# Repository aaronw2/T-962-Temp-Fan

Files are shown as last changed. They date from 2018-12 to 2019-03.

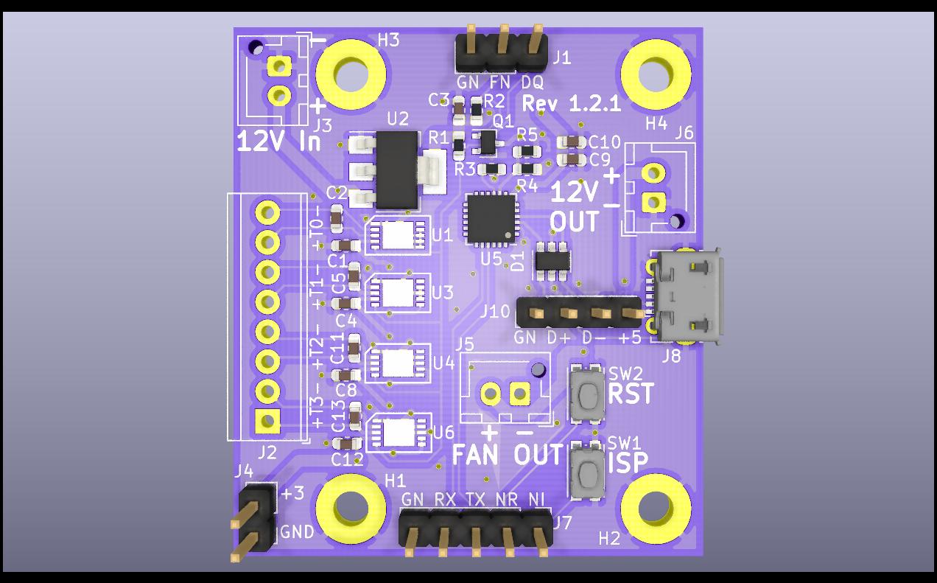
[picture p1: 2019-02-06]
Pictures/Front.jpg

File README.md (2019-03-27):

This board provides support for up to 4 K-type temperature probes as
well as fan PWM support and a USB to serial interface to enhance the
T-962 reflow oven.

Connectors:

J1: Connect to T962 controller board
1: DQ
2: FAN_PWM
3: GND

J2: Thermocouple connector
1: T3+
2: T3-
3: T2+
4: T2-
5: T1+
6: T1-
7: T0+
8: T0-

J3: 12V in
1: GND
2: +12V

J4: +3V out
1: GND
2: +3V

J5: Fan out
1: PWM (GND)
2: +12V

J6: +12V out
1: GND
2: +12V

J7: Programming Header, connect to T962 controller board header
1: N_ISP
2: N_RST
3: TX
4: RX
5: GND

Hook up either J8 or J10, not both

J8: Micro USB

J9: N_ISP and N_RST for external buttons
1: N_RST
2: GND
3: N_ISP

J10: USB
1: GND
2: D+
3: D-
4: +5V

BOM:
QTY Ref
5   C1,C4,C8,C10,C12: 0.1uf X7R 0603
4   C2,C5,C11,C13 0.01uF X7R 0603
1   C3 1uF X7R 0603
1   C9 4.7uF X7R 0603
1   D1: ST Microelectronics USBLC6-2SC6
1   J2: TE 282834-8
1   J3, J5, J6: JST XH-B02B-XH-AM
1   J8: Molex 105017-0001
1   Q1: Infineon BSS214NWH6327XTSA1
1   R1: 4.7K 0603
1   R2: 100K 0603
1   R3: 1K 0603
1   R4: 22.1K 0603
1   R5: 47.5K 0603
2   S1, S2: C&K KMR231NG LFS
4   U1, U3, U4, U6: Maxim MAX31850KATB+
1   U2: ST Microelectronics LD1117S33CTR
1   U5: Silicon Labs CP2102N-A01-QFN24

All parts can be found at Digikey, however the MAX31850KATB+ is considerably
less expensive at Mouser.

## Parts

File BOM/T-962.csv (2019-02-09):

Refs | Value | Footprint | Quantity | MFR | MPN | SPR | SPN
U5 | CP2102N-A01-QFN24 | Aaron:QFN-24-1EP_4x4mm_Pitch0.5mm_rounded_corners | 1 | Silicon Labs | CP2102N-A01-GQFN24R | Digikey | 336-4737-1-ND
SW1;SW2 | SW_SPST_KMR2 | Aaron:SW_SPST_KMR2 | 2 | C&K | KMR231NG LFS | Digikey | CKN10246CT-ND
U1;U3;U4;U6 | MAX31850KATB+ | Aaron:TDFN-10_3x4mm_P0.5mm | 4 | Maxim | MAX31850KATB+ | Digikey | MAX31850KATB+-ND
J8 | USB_B_Micro | Aaron:USB_Micro-B_Molex-105017-0001 | 1 | Molex | 1050170001 | Digikey | WM1399CT-ND
C2;C5;C11;C13 | 0.01uF | Capacitor_SMD:C_0603_1608Metric | 4 | - | - | - | -
C1;C4;C8;C12;C10 | 0.1uF | Capacitor_SMD:C_0603_1608Metric | 5 | - | - | - | -
C3 | 1uF | Capacitor_SMD:C_0603_1608Metric | 1 | - | - | - | -
C9 | 4.7uF | Capacitor_SMD:C_0603_1608Metric | 1 | - | - | - | -
J3;J5;J6 | JST XH-B02B-XH-AM | Connector_JST:JST_XH_B02B-XH-AM_1x02_P2.50mm_Vertical | 3 | JST | B2B-XH-A(LF)(SN) | Digikey | 455-2247-ND
J4 | Conn_01x02_Male | Connector_PinHeader_2.54mm:PinHeader_1x02_P2.54mm_Vertical | 1 | - | - | - | -
J1 | Conn_01x03 | Connector_PinHeader_2.54mm:PinHeader_1x03_P2.54mm_Vertical | 1 | - | - | - | -
J10 | Conn_01x04 | Connector_PinHeader_2.54mm:PinHeader_1x04_P2.54mm_Vertical | 1 | - | - | - | -
J7 | 2.54mm pin header | Connector_PinHeader_2.54mm:PinHeader_1x05_P2.54mm_Vertical | 1 | - | - | - | -
H1;H2;H3;H4 | MountingHole_Pad | MountingHole:MountingHole_3mm_Pad | 4 | - | - | - | -
U2 | LD1117S33CTR | Package_TO_SOT_SMD:SOT-223 | 1 | STMicroelectronics | LD1117S33CTR | Digikey | 497-1241-1-ND
D1 | USBLC6-2SC6 | Package_TO_SOT_SMD:SOT-23-6 | 1 | STMicroelectronics | USBLC6-2SC6 | Digikey | 497-5235-1-ND
Q1 | BSS214NW | Package_TO_SOT_SMD:SOT-323_SC-70 | 1 | Infineon | BSS214NWH6327XTSA1 | Digikey | BSS214NWH6327XTSA1CT-ND
R2 | 100K | Resistor_SMD:R_0603_1608Metric | 1 | Yageo | AC0603FR-07100KL | Digikey | 311-100KLDCT-ND
R3 | 1K | Resistor_SMD:R_0603_1608Metric | 1 | Yageo | RC0603FR-071KL | Digikey | 311-1.00KHRCT-ND
R4 | 22.1K | Resistor_SMD:R_0603_1608Metric | 1 | Panasonic | ERJ-3EKF2212V | Digikey | P22.1KHCT-ND
R1 | 4.7K | Resistor_SMD:R_0603_1608Metric | 1 | Yageo | RC0603FR-074K7L | Digikey | 311-4.70KHRCT-ND
R5 | 47.5K | Resistor_SMD:R_0603_1608Metric | 1 | Yageo | RC0603FR-0747K5L | Digikey | 311-47.5KHRCT-ND
J2 | TE 282834-8 | TerminalBlock_TE-Connectivity:TerminalBlock_TE_282834-8_1x08_P2.54mm_Horizontal | 1 | TE | 282834-8 | Digikey | A98338-ND

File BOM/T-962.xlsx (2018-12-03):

Refs | Value | Footprint | Quantity | MFR | MPN | SPR | SPN
U5 | CP2102N-A01-QFN24 | Aaron:QFN-24-1EP_4x4mm_Pitch0.5mm_rounded_corners | 1 | Silicon Labs | CP2102N-A01-GQFN24R | Digikey | 336-4737-1-ND
SW1;SW2 | SW_SPST_KMR2 | Aaron:SW_SPST_KMR2 | 2 | C&K | KMR231NG LFS | Digikey | CKN10246CT-ND
U1;U3;U4;U6 | MAX31850KATB+ | Aaron:TDFN-10_3x4mm_P0.5mm | 4 | Maxim | MAX31850KATB+ | Digikey | MAX31850KATB+-ND
J8 | USB_B_Micro | Aaron:USB_Micro-B_Molex-105017-0001 | 1 | Molex | 1050170001 | Digikey | WM1399CT-ND
C2;C5;C11;C13 | 0.01uF | Capacitor_SMD:C_0603_1608Metric | 4 | Samsung | CL10B103KB8NCNC | Digikey | 1276-1921-1-ND
C1;C4;C8;C12;C7;C10 | 0.1uF | Capacitor_SMD:C_0603_1608Metric | 6 | Samsung | CL10B104KO8WPNC | Digikey | 1276-6582-1-ND
C3 | 1uF | Capacitor_SMD:C_0603_1608Metric | 1 | Samsung | CL10B105MO8NNWC | Digikey | 1276-6524-1-ND
C6;C9 | 4.7uF | Capacitor_SMD:C_0603_1608Metric | 2 | Samsung | CL10B475KQ8NQNC | Digikey | 1276-2087-1-ND
J3;J5 | B2B-XH-A(LF)(SN) | Connector_JST:JST_XH_B02B-XH-AM_1x02_P2.50mm_Vertical | 2 | JST | B2B-XH-A(LF)(SN) | Digikey | 455-2247-ND
J1 | 2.54mm pin header | Connector_PinHeader_2.54mm:PinHeader_1x03_P2.54mm_Vertical | 1 | - | - | - | -
J10 | Conn_01x04 | Connector_PinHeader_2.54mm:PinHeader_1x04_P2.54mm_Vertical | 1 | - | - | - | -
J7 | 2.54mm pin header | Connector_PinHeader_2.54mm:PinHeader_1x05_P2.54mm_Vertical | 1 | - | - | - | -
H1;H2;H3;H4 | MountingHole_Pad | MountingHole:MountingHole_3mm_Pad | 4 | - | - | - | -
U2 | LD1117S33CTR | Package_TO_SOT_SMD:SOT-223 | 1 | ST Microelectronics | LD1117S33CTR | Digikey | 497-1241-1-ND
Q1 | BSS214NW | Package_TO_SOT_SMD:SOT-323_SC-70 | 1 | Infineon | BSS214NWH6327XTSA1 | Digikey | BSS214NWH6327XTSA1CT-ND
D1 | USBLC6-2SC6 | Package_TO_SOT_SMD:SOT-666 | 1 | STMicroelectronics | USBLC6-2SC6 | Digikey | 497-5235-1-ND
R2 | 100K | Resistor_SMD:R_0603_1608Metric | 1 | Yageo | AC0603FR-07100KL | Digikey | 311-100KLDCT-ND
R3 | 1K | Resistor_SMD:R_0603_1608Metric | 1 | Yageo | RC0603FR-071KL | Digikey | 311-1.00KHRCT-ND
R4 | 22.1K | Resistor_SMD:R_0603_1608Metric | 1 | Panasonic | ERJ-3EKF2212V | Digikey | P22.1KHCT-ND
R1 | 4.7K | Resistor_SMD:R_0603_1608Metric | 1 | Yageo | RC0603FR-074K7L | Digikey | 311-4.70KHRCT-ND
R5 | 47.5K | Resistor_SMD:R_0603_1608Metric | 1 | Yageo | RC0603FR-0747K5L | Digikey | 311-47.5KHRCT-ND
J2 | TE 282834-8 | TerminalBlock_TE-Connectivity:TerminalBlock_TE_282834-8_1x08_P2.54mm_Horizontal | 1 | TE | 282834-8 | Digikey | A98338-ND

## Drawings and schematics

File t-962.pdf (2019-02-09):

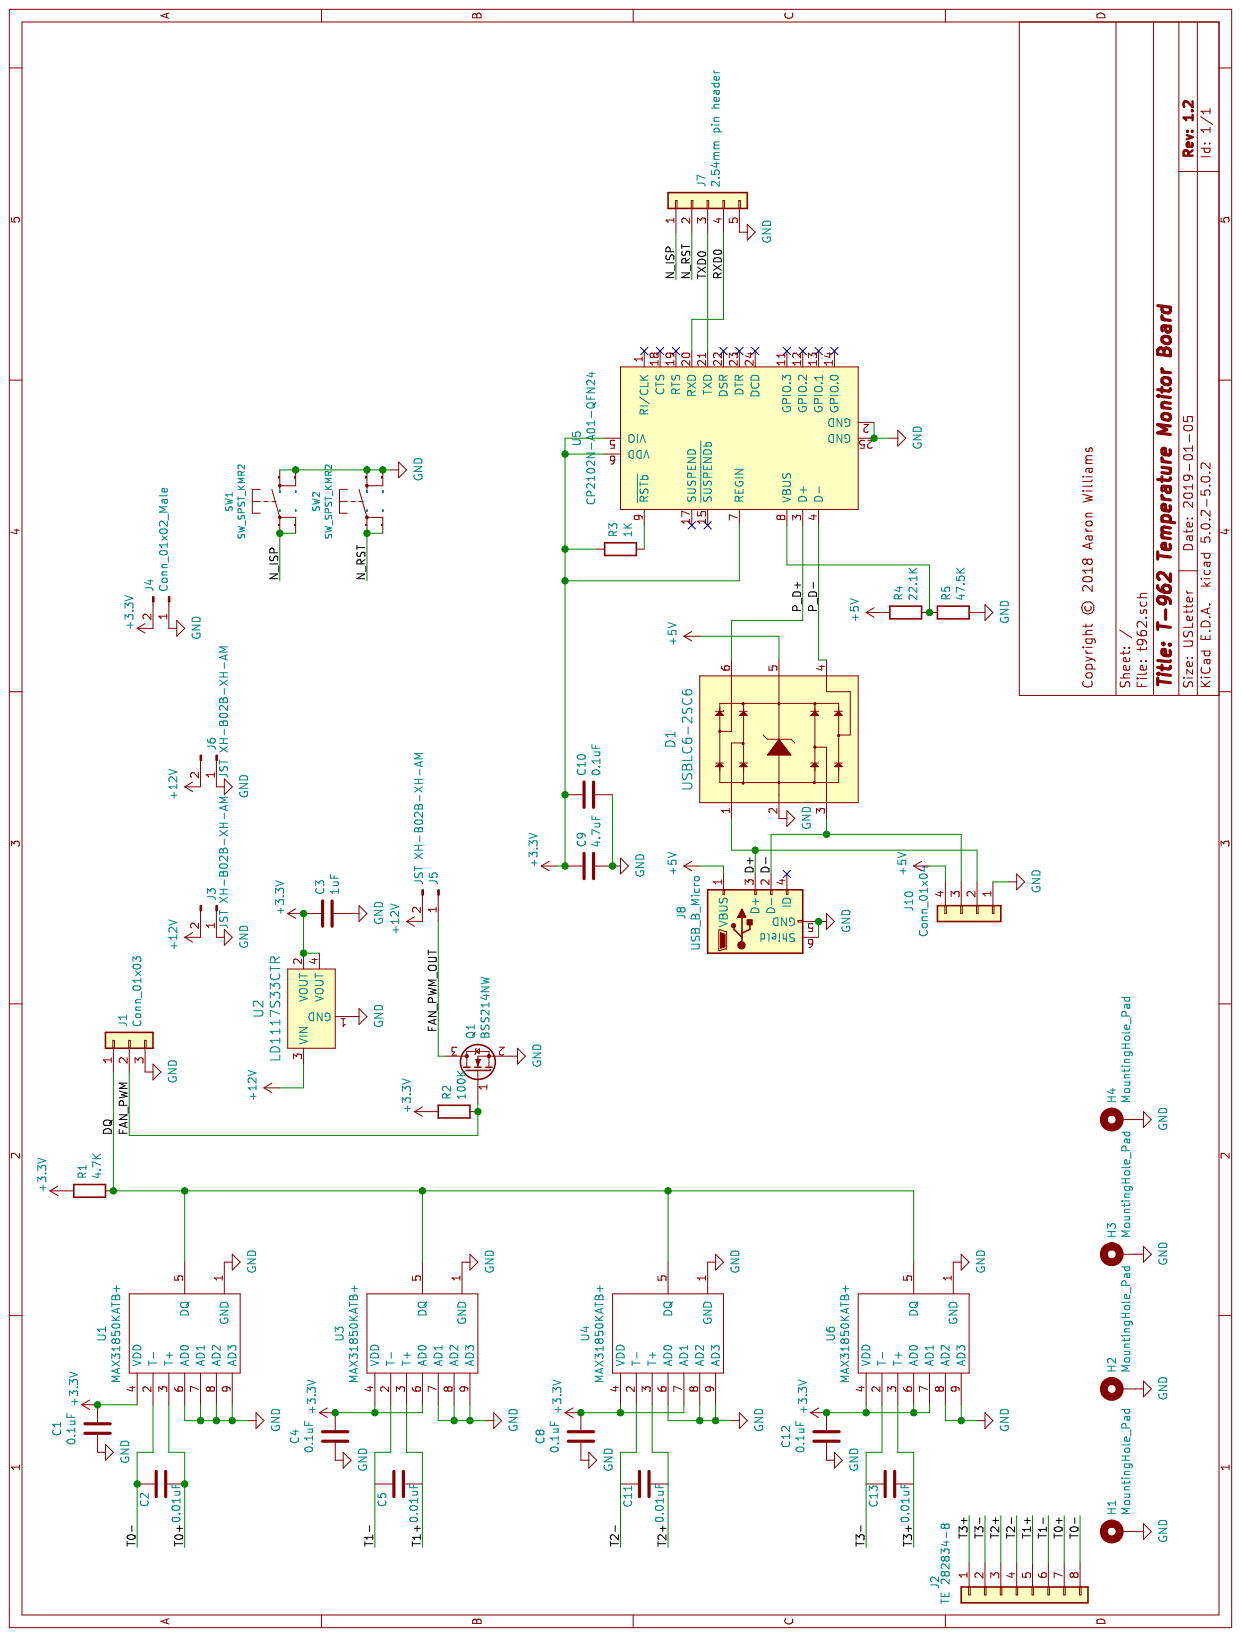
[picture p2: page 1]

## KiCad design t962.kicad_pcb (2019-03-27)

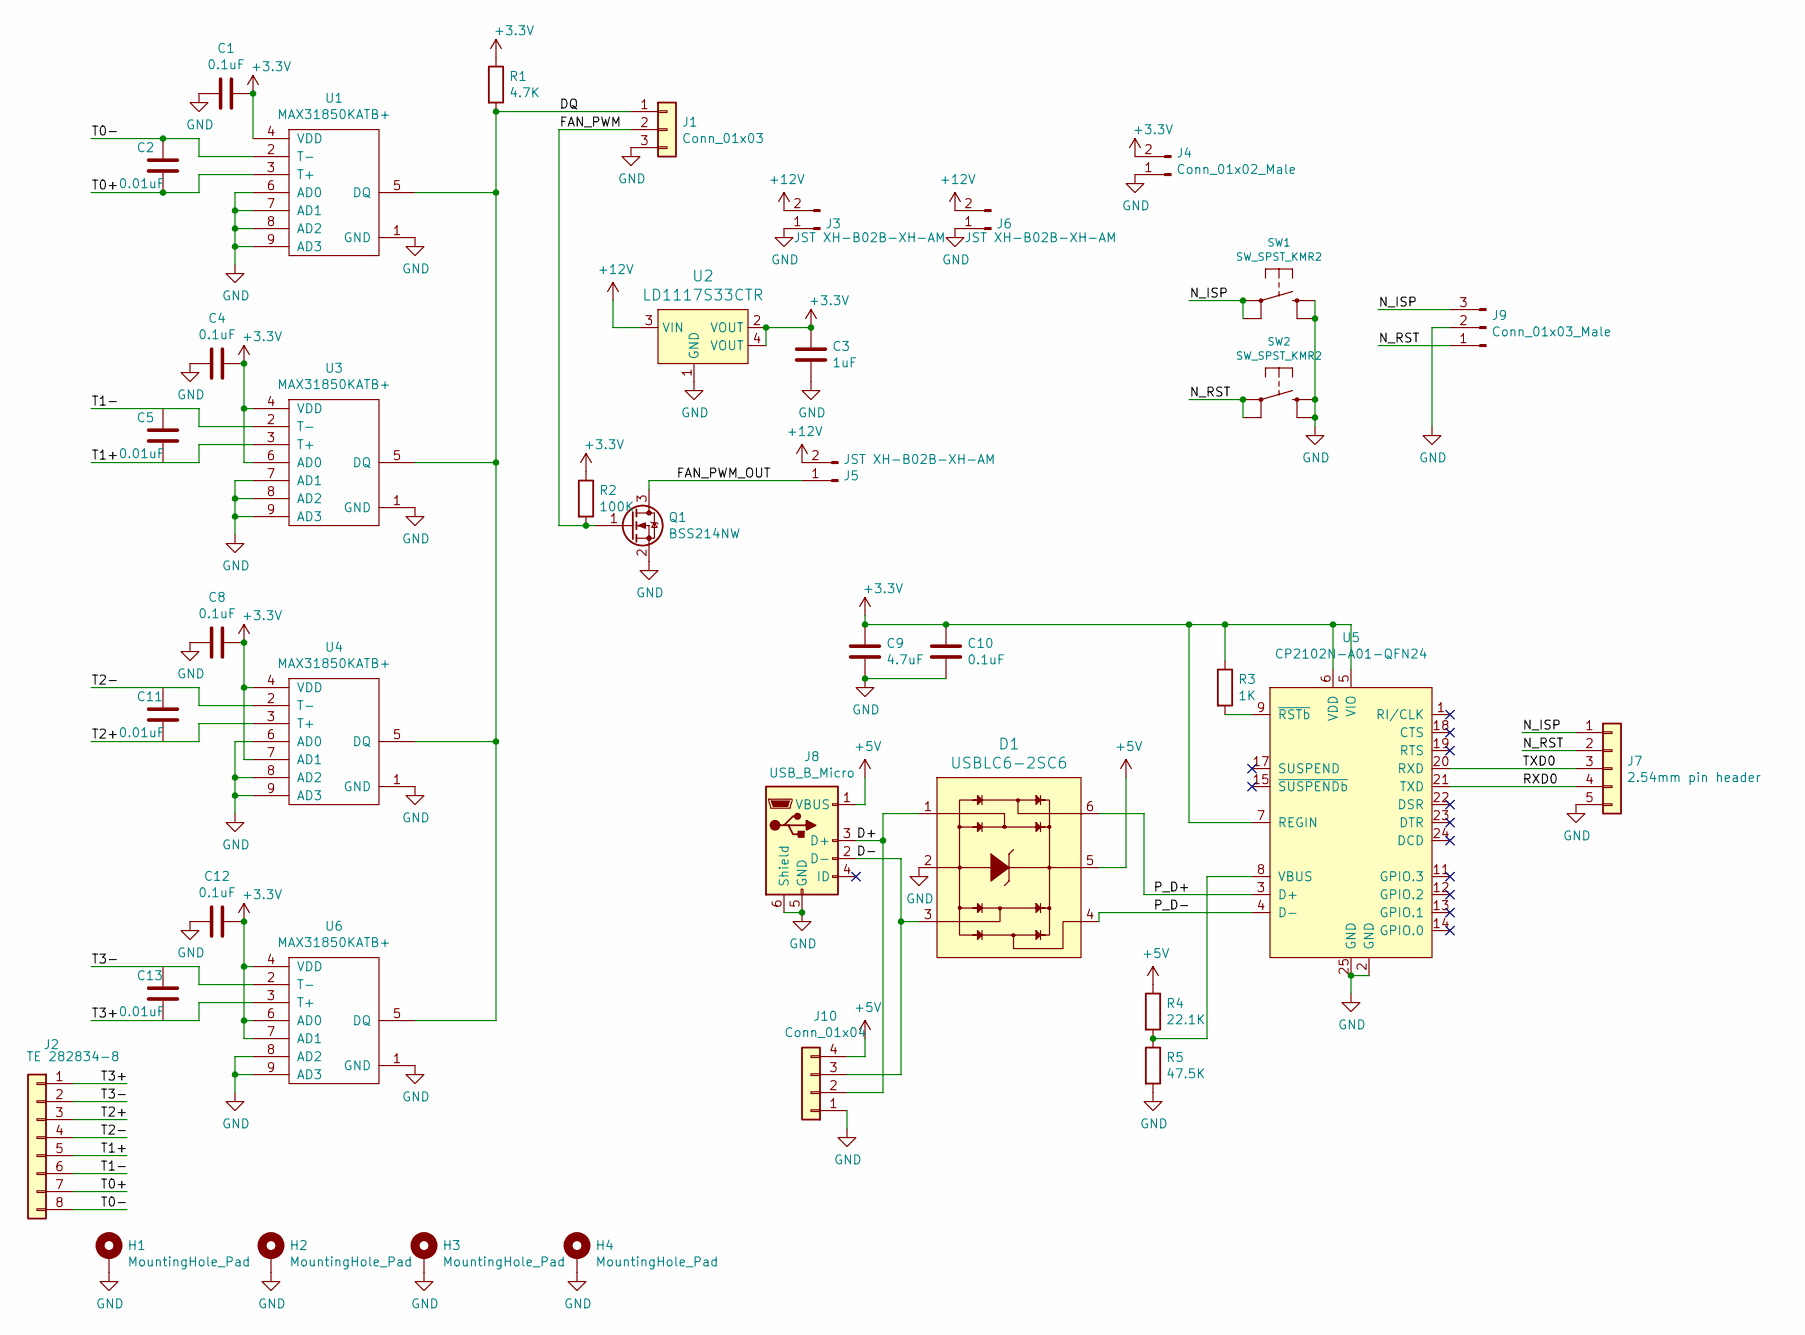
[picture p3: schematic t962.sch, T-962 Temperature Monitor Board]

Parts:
C1, C4, C8, C10, C12: 0.1uF; C_0603_1608Metric
C2, C5, C11, C13: 0.01uF; C_0603_1608Metric
C3: 1uF; C_0603_1608Metric
C9: 4.7uF; C_0603_1608Metric
D1: USBLC6-2SC6; SOT-23-6; MPN USBLC6-2SC6; Digi-Key_PN 497-5235-1-ND
H1, H2, H3, H4: MountingHole_Pad; MountingHole_3mm_Pad
J1: Conn_01x03; PinHeader_1x03_P2.54mm_Vertical
J2: TE 282834-8; TerminalBlock_TE_282834-8_1x08_P2.54mm_Horizontal; MPN 282834-8
J3, J5, J6: JST XH-B02B-XH-AM; JST_XH_B02B-XH-AM_1x02_P2.50mm_Vertical; MPN B2B-XH-A(LF)(SN)
J4: Conn_01x02_Male; PinHeader_1x02_P2.54mm_Vertical
J7: 2.54mm pin header; PinHeader_1x05_P2.54mm_Vertical
J8: USB_B_Micro; USB_Micro-B_Molex-105017-0001; MPN 1050170001
J9: Conn_01x03_Male; PinHeader_1x03_P2.54mm_Vertical
J10: Conn_01x04; PinHeader_1x04_P2.54mm_Vertical
Q1: BSS214NW; SOT-323_SC-70; MPN BSS214NWH6327XTSA1
R1: 4.7K; R_0603_1608Metric; MPN RC0603FR-074K7L
R2: 100K; R_0603_1608Metric; MPN AC0603FR-07100KL
R3: 1K; R_0603_1608Metric; MPN RC0603FR-071KL
R4: 22.1K; R_0603_1608Metric; MPN ERJ-3EKF2212V
R5: 47.5K; R_0603_1608Metric; MPN RC0603FR-0747K5L
SW1, SW2: SW_SPST_KMR2; MPN KMR231NG LFS
U1, U3, U4, U6: MAX31850KATB+; TDFN-10_3x4mm_P0.5mm; MPN MAX31850KATB+
U2: LD1117S33CTR; SOT-223; MPN LD1117S33CTR; Digi-Key_PN 497-1241-1-ND
U5: CP2102N-A01-QFN24; QFN-24-1EP_4x4mm_Pitch0.5mm_rounded_corners; MPN CP2102N-A01-GQFN24R

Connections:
+3V3: C1.2, C3.1, C4.2, C8.2, C9.1, C10.1, C12.2, J4.2, R1.1, R2.1, R3.1, U1.4 (VDD), U2.2 (VOUT), U2.4 (VOUT), U3.4 (VDD), U3.6 (AD0), U4.4 (VDD), U4.7 (AD1), U5.5 (VIO), U5.6 (VDD), U5.7 (REGIN), U6.4 (VDD), U6.6 (AD0), U6.7 (AD1)
+5V: D1.5, J8.1 (VBUS), J10.4, R4.1
+12V: J3.2, J5.2, J6.2, U2.3 (VIN)
/D+: D1.1, J8.3 (D+), J10.2
/D-: D1.3, J8.2 (D-), J10.3
/DQ: J1.1, R1.2, U1.5 (DQ), U3.5 (DQ), U4.5 (DQ), U6.5 (DQ)
/FAN_PWM: J1.2, Q1.1 (G), R2.2
/FAN_PWM_OUT: J5.1, Q1.3 (D)
/N_ISP: J7.1, J9.3, SW1.1
/N_RST: J7.2, J9.1, SW2.1
/P_D+: D1.6, U5.3 (D+)
/P_D-: D1.4, U5.4 (D-)
/RXD0: J7.4, U5.21 (TXD)
/T0+: C2.1, J2.7, U1.3 (T+)
/T0-: C2.2, J2.8, U1.2 (T-)
/T1+: C5.1, J2.5, U3.3 (T+)
/T1-: C5.2, J2.6, U3.2 (T-)
/T2+: C11.1, J2.3, U4.3 (T+)
/T2-: C11.2, J2.4, U4.2 (T-)
/T3+: C13.1, J2.1, U6.3 (T+)
/T3-: C13.2, J2.2, U6.2 (T-)
/TXD0: J7.3, U5.20 (RXD)
GND: C1.1, C3.2, C4.1, C8.1, C9.2, C10.2, C12.1, D1.2, H1.1, H2.1, H3.1, H4.1, J1.3, J3.1, J4.1, J6.1, J7.5, J8.5 (GND), J8.6 (Shield), J9.2, J10.1, Q1.2 (S), R5.2, SW1.2 (S), SW2.2 (S), U1.1 (GND), U1.6 (AD0), U1.7 (AD1), U1.8 (AD2), U1.9 (AD3), U1.11 (GND), U2.1 (GND), U3.1 (GND), U3.7 (AD1), U3.8 (AD2), U3.9 (AD3), U3.11 (GND), U4.1 (GND), U4.6 (AD0), U4.8 (AD2), U4.9 (AD3), U4.11 (GND), U5.2 (GND), U5.25 (GND), U6.1 (GND), U6.8 (AD2), U6.9 (AD3), U6.11 (GND)
unnamed: R3.2, U5.9 (~RSTb)
unnamed: R4.2, R5.1, U5.8 (VBUS)

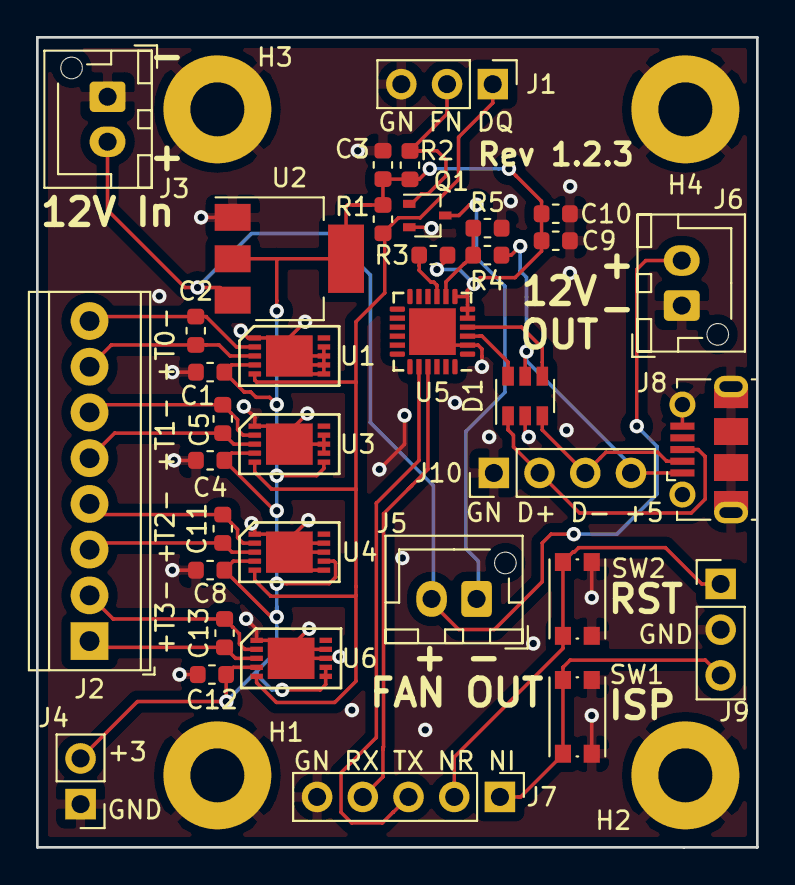
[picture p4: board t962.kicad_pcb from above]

Board: 2 copper layers, 40.0 x 45.0 mm, 40 parts (0 on the bottom side), 25 nets.

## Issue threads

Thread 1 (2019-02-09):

Can you provide a PDF of the schematic please

rolandking, 2019-02-09:
Looks like a nice project - thanks very much for sharing it.

Attempting to load up in kicad I have version mismatches and library issues which I suspect might not be that uncommon (I'm still on kicad 4.x). You provide the gerbers which is great, can you PDF up the schematic and upload that too please so people without kicad, or without a compatible version of kicad, can read, understand and build the project.

Thanks very much.

aaronw2, 2019-02-09:
Done. Note that my gerbers may have been out of date and I may have screwed up on the minimum solder mask width. Anyway, all should be good now and I also included a PDF of the schematic. This was done using KiCad 5.0.2 and I have my own libraries for some of these parts.

All parts can be found on Digikey, though the MAX31850s are a lot cheaper from Mouser.

Closed 2019-02-09.

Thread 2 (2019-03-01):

RXD/TXD maybe flipped?

metaneutrons, 2019-03-01:
Hi there, thanks for sharing your board. I already forked it and wonder if you maybe have flipped RXD/TXD connected to CP2102N? All other schematics have TX/RX crossed...

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

aaronw2, 2019-03-01:
Hi,

It's possible. I haven't had time to try and test that part out. It's easy to fix that in post fortunately, but I'll make the change.

-Aaron

aaronw2, 2019-03-27:
I have swapped TX and RX in rev 1.2.3 in addition to bringing out N_ISP and N_RST to another connector. No changes are required for the template.

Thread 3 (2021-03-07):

What happend on F3 page with 4 TC connected ?

zian31, 2021-03-07:
Hi,
If possible, have you a photo of the T-962 LCD (UnifiedEngineering) F3 page (Manual Mode) with 4 TC connected (and no DS18B20 connected for cold junction) ?
The AIR LEFT and RIGHT temperatures should be presents, but can we also see TRAY LEFT and RIGHT temp ?
An average of AIR LEFT & RIGHT is also shown ? Or an average of the 4 TC ?
Or maybe an average of the TRAY LEFT & RIGHT, which should be logical (moreover if this average is taken as the Temperature for the PID).
Thanks a lot for your answer, I'm asking it before making this modification.

zian31, 2021-03-10:
Answered here : https://github.com/UnifiedEngineering/T-962-improvements/issues/157

Closed 2021-03-10.

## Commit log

2018-11-17 Initial commit.
    [T-962.csv, T-962.xlsx, t962.kicad_pcb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]
2018-11-18 Added more part number information.
    [t962.sch]
2018-12-03 Fixed 12V connectors and USB to serial
    This swaps +12 and GND on the 12V and fan connectors and adds a second
    12v connector for bypassing the fan control if desired. Additionally,
    the SI2102N is now powered from the 3.3V supply instead of the USB bus.
    Updated to revision 1.1.
    [t962.kicad_pcb, t962.sch]
2018-12-03 Updated BOM
    [T-962.xlsx, t962.kicad_pcb, t962.sch]
2018-12-03 Added gerber files.
    [t962-B.Cu.gbr, t962-B.Mask.gbr, t962-B.SilkS.gbr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]
2019-01-05 This fixes the VIO input so it is properly powered. Additionally, the footprint for the USBLC6-2SC6 has been fixed to a SOT23-6 which is a bigger footprint than the SOT666 that was there.
    [t962-B.Cu.gbr, t962-B.Mask.gbr, t962-B.SilkS.gbr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]
2019-01-26 Fixed solder mask clearance.
    [t962.kicad_pcb]
2019-02-06 Fixed solder mask again and included pictures.
    [t962.kicad_pcb]
2019-02-09 Fixed pad mask clearance.
    [t962.kicad_pcb]
2019-02-09 Added PDF of schematic.
2019-02-09 Fixed solder mask min width again.
    [t962.kicad_pcb]
2019-02-09 Updated gerbers to match.
    [t962-B.Cu.gbr, t962-B.Mask.gbr, t962-B.SilkS.gbr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]
2019-03-27 Swap TX/RX and add connector to expose RST and NI
    TX and RX were swapped from what they should be. This
    fixes that. Additionally, J9 was added so that external
    buttons can be added for NI and RST.
    [t962-B_Cu.gbr, t962-B_Mask.gbr, t962-B_SilkS.gbr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]
2019-03-27 Forgot to save changes for rev 1.2.3
    [t962.kicad_pcb, t962.sch]

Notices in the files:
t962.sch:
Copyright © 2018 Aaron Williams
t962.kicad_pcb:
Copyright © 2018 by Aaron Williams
